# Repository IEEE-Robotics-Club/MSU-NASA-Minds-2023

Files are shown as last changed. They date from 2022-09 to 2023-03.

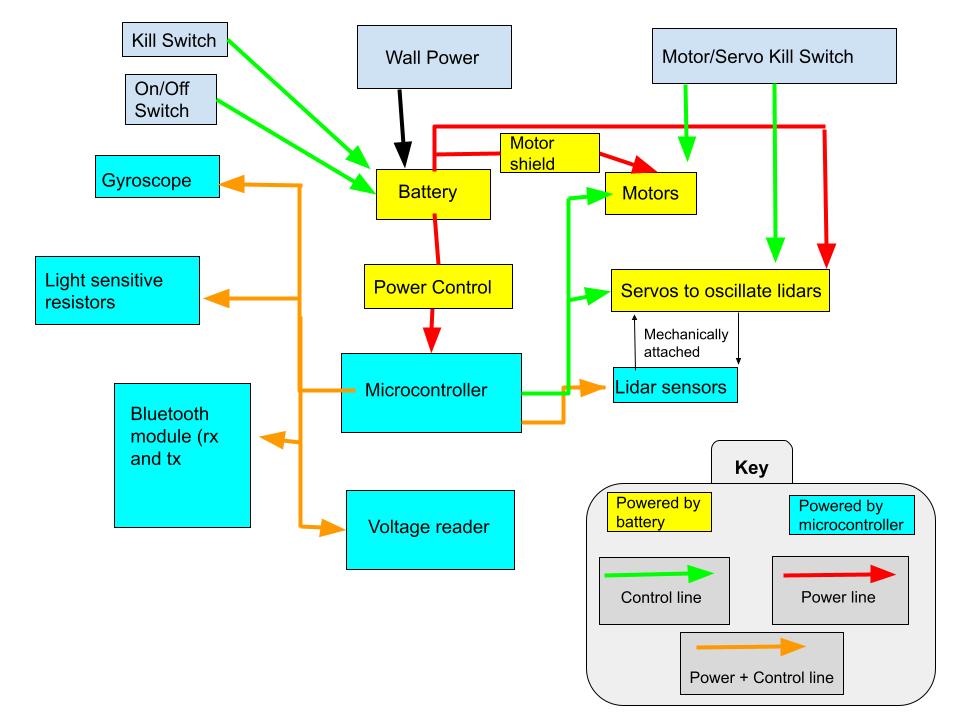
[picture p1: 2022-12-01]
Docs/iteration1/Electrical Block Diagram V2.jpg

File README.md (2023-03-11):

# MSU-NASA-Minds-2023
The code repository for the 2023 MSU NASA Minds competition. This year we will explore different cooperative imformation gathering techniques via simulation and building a homogenous robotic swarm. This repository will be split up into several different sections:

## ARGoS Robotic Swarm Simulator: 

We will be modelling and testing our system methods using ARGoS Robotic Simulator. This will serve the purpose of testing our movement algorithms and swarm logic.  

### Getting Started with ARGoS Simulator on an Ubuntu Machine:

1. Install ARGoS as per directions here https://www.argos-sim.info/core.php 

2. Clone the ARGoS-Simulations Repository and save it in a memorable place. 

3. Navigate to the repository using the terminal and run the command:

  `$ argos3 -c  Tellus-Prototype/tellus.argos

This will run the example simulation and also open the Lua editor where you can change the Robot's behaviour with a Lua Script.

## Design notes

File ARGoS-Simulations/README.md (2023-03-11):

# Getting Started with ARGoS Robotic Simulator 

After installing ARGoS Simulatior, run this command to launch the demo project:

`
$ argos3 -c  Tellus-Prototype/tellus.argos
`

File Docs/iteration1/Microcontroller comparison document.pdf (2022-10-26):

Microcontroller comparison document-

Seeed Studio XIAO nRF52840

Teensy 4.1

Pros: Teensy

- Has better software support (open source OS prebuilt on GitHub)
- Has more RAM (2 banks 512k)
- Has a FPU
- Decent hardware documentation compared to Xiao

Cons: Teensy

- Overheating with the main chip
- More expensive ($29.60)
- Sometimes no USB communication

Pros: Xiao

- Onboard bluetooth support (good for comms)
- Cheaper ($9.90)

Cons: Xiao

- No open source OS (would have to build our own)
- Poor documentation compared to teensy

Winner:

Documentation on the teensy is better compared to xiao, and the support of an OS makes it a lot better to work with. We can overcome the lack of onboard wireless support by using an external module.

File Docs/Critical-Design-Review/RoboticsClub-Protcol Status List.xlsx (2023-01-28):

Protocol lists of what is created and what is not | Protcol Flowchart Exist? | Other known names | Who made it/Where can it be Found?
Name of Protocol |  | Other name | Name and/or where it is
Boot up Calibration
Sector assignment
Agent Update |  | Swarm State Detection
Open Rescue Request
Close Rescue Request
Rescue attempt |  | Rescue Detection Protocol
Assist Path
GPR Path Generation
Collect and Store GPR
Fault Detection Protocol

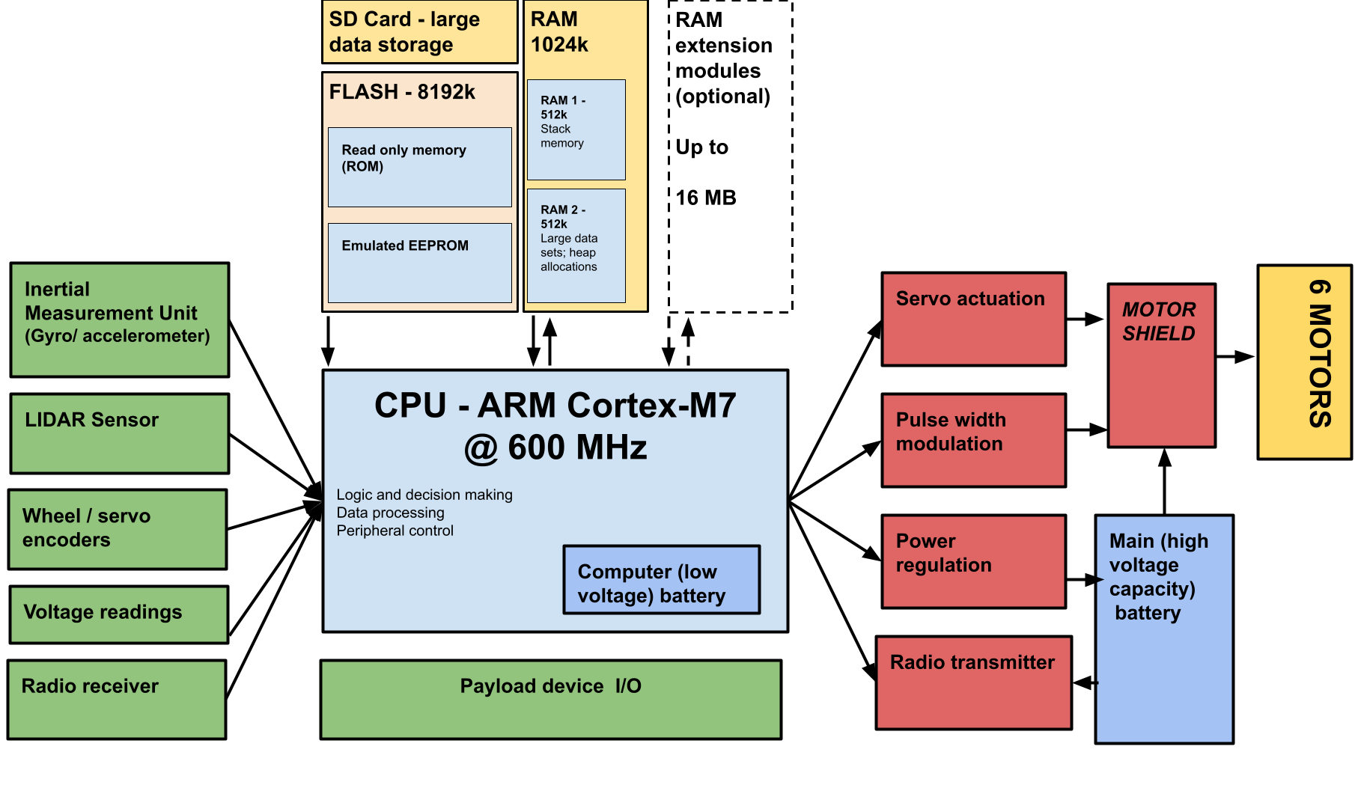
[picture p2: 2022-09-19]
Docs/iteration1/embedded systems diagram.png

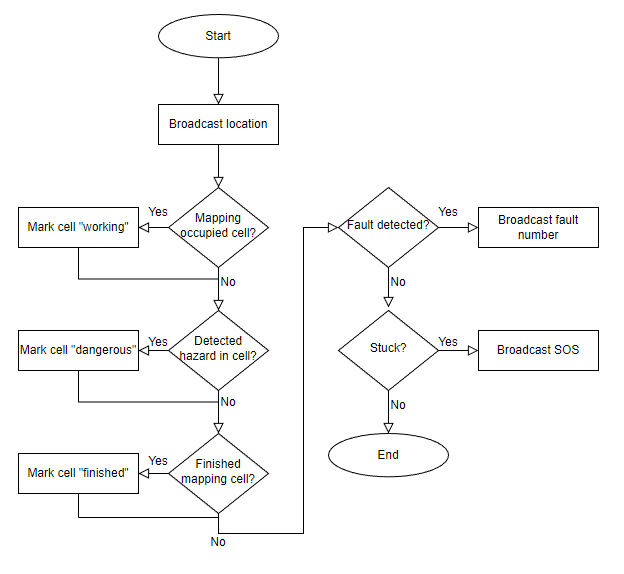
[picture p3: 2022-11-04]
Docs/iteration1/Send Communication Protocol.png

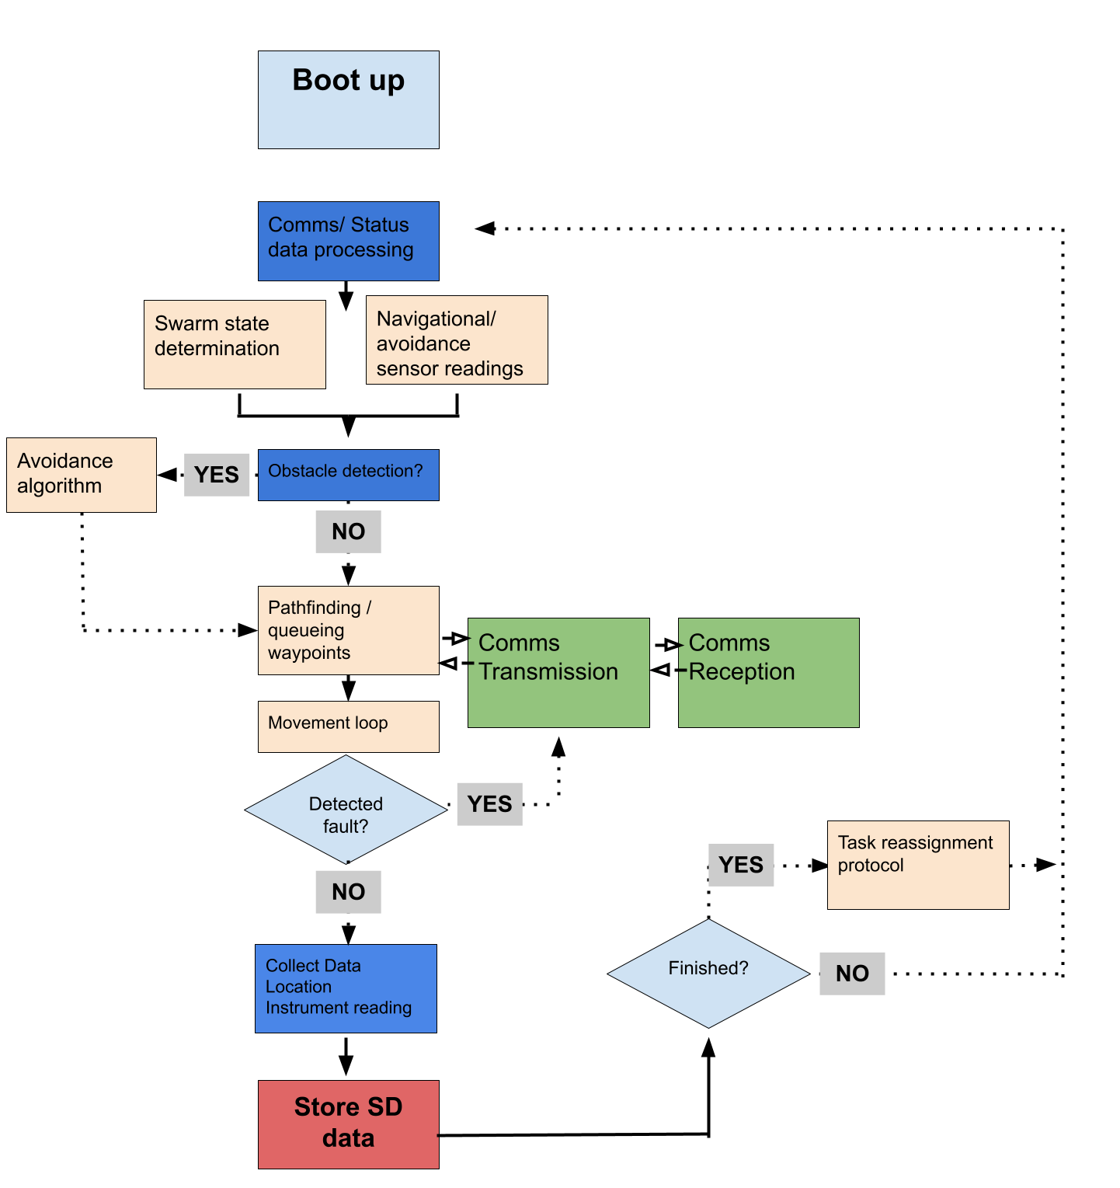
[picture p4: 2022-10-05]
Docs/iteration1/Protocol Flowchart Iteration 1.png

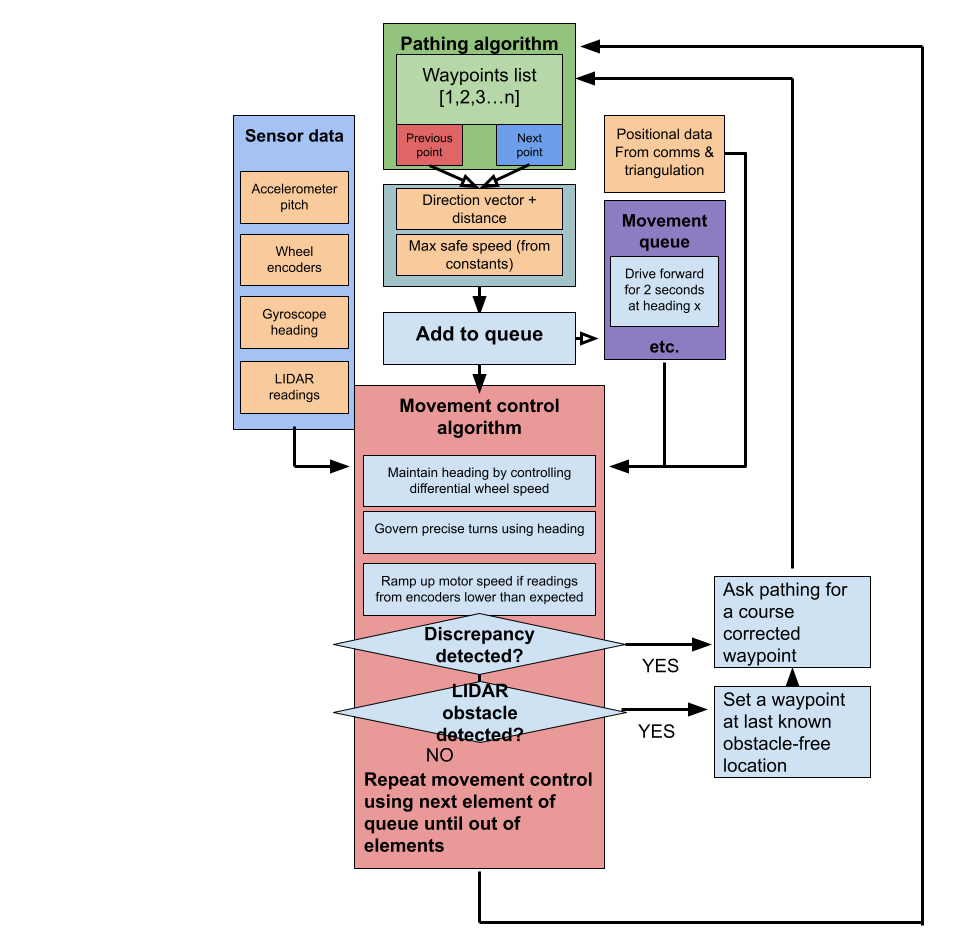
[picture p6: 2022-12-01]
Docs/iteration1/Movement control sub-protocol.png

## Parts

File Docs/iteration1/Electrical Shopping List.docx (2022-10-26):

Pack of 8 motors - $12 (https://www.amazon.com/Electric-Prewired-Intelligent-Chassis-Connector/dp/B0B19VC1VL?hvadid=598295292427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)

Speed | 18000 RPM
Item Weight | 29 Grams

8PCSTT motor robot gear motor operating voltage: 3V~12VDC (recommended operating voltage of about 6 to 8V) with 2×200mm wires

Operating Voltage: 3V~6VDC; Batch Number: Double axis 1:48; Load Current: ≤150mA (200mA MAX)

Maximum torque: 800gf cm min (3V) ; No-load speed: 1:48 (3V time)

Pack of 8 servos - $20 (https://www.amazon.com/10Pcs-Servos-Helicopter-Airplane-Controls/dp/B08KY49SFX?hvadid=475740798427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)

Weight: 9g

Stall torque: 1.8kg/cm

Operating speed: 0.1sec/60degree

Operating voltage: 4.8V

Temperature range: 0℃ ~ +55℃

Dead band width: 10us

Maximum rotation angle: 180 degrees

Gear medium: nylon

Working mode: Simulation

Circuit connection:

Yellow line (signal line)

Red line (power line)

Brown (ground)

Lipo charger $7, will need four max (https://www.adafruit.com/product/1904)

Charges 4.7v Lipo batteries of any capacity

LiPo Battery $12.5 (https://www.adafruit.com/product/2011), will need two

- Dimensions: 60mm x 36mm x 7mm / 2.4" x 1.4" x 0.3"
- Weight: 34g
- Nominal Capacity: 2000mAh ±2%
- Nominal Voltage: 3.7V
- Standard Charge Current: ~0.2C / 0.5A
- Charge Cut-Off Voltage: 4.2V
- Standard Discharge Current: ~0.2C / 0.5A
- Battery Datashee (https://cdn-shop.adafruit.com/datasheets/LiIon2000mAh37V.pdf)t

TOTAL PRICE: $85 (before tax) ~$100 after tax

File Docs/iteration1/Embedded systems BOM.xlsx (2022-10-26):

Name | Cost | Quantity | Total Cost: | $152.59
Teensy 4.1 | $34.60 | 1 | $34.60
USB | $0.00 | 1 | $0.00
SD card | $11.25 | 1 | $11.25
Pin headers | $4.99 | 1 | $4.99
Bluetooth | $20.00 | 1 | $20.00
LIDAR Module | $24.90 | 1 | $24.90
Wheel encoder x2 | $13.95 | 3 | $41.85
Motor shield | $15.00 | 1 | $15.00

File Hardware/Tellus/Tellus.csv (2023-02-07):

Comment | Designator | Footprint | LCSC
22uF | C1,C3,C5,C6,C8 | Capacitor_SMD:C_1210_3225Metric_Pad1.33x2.70mm_HandSolder | C309062
0.1uF | C2,C9 | Capacitor_SMD:C_1210_3225Metric_Pad1.33x2.70mm_HandSolder | C106103
10n | C4 | Capacitor_SMD:C_1210_3225Metric_Pad1.33x2.70mm_HandSolder | C527379
2.22uF | C7 | Capacitor_SMD:C_1210_3225Metric_Pad1.33x2.70mm_HandSolder | C76681
10K | R1 | Resistor_SMD:R_1206_3216Metric | C416174
4.7k | R2,R3,R4 | Resistor_SMD:R_1206_3216Metric | C104821
A3909 | U1,U3,U4 | Package_SO:SSOP-10_3.9x4.9mm_P1.00mm | C2653462
AMS1117-3.3 | U2 | Package_TO_SOT_SMD:SOT-89-3 | C347256

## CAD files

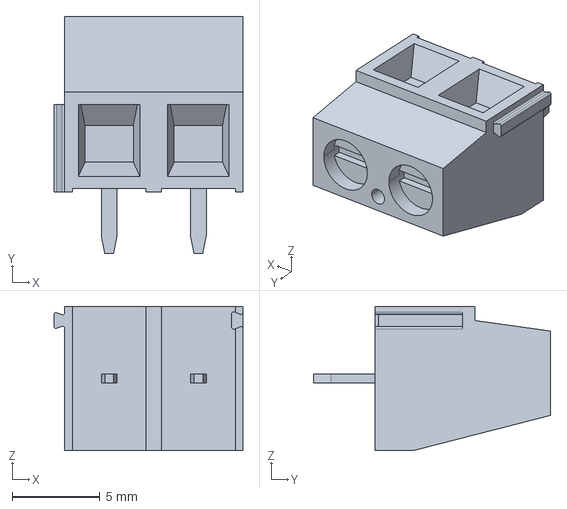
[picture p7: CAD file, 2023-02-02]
Hardware/Tellus/Terminal Block/282837-2.step
10.8 x 13.5 x 8.20 mm

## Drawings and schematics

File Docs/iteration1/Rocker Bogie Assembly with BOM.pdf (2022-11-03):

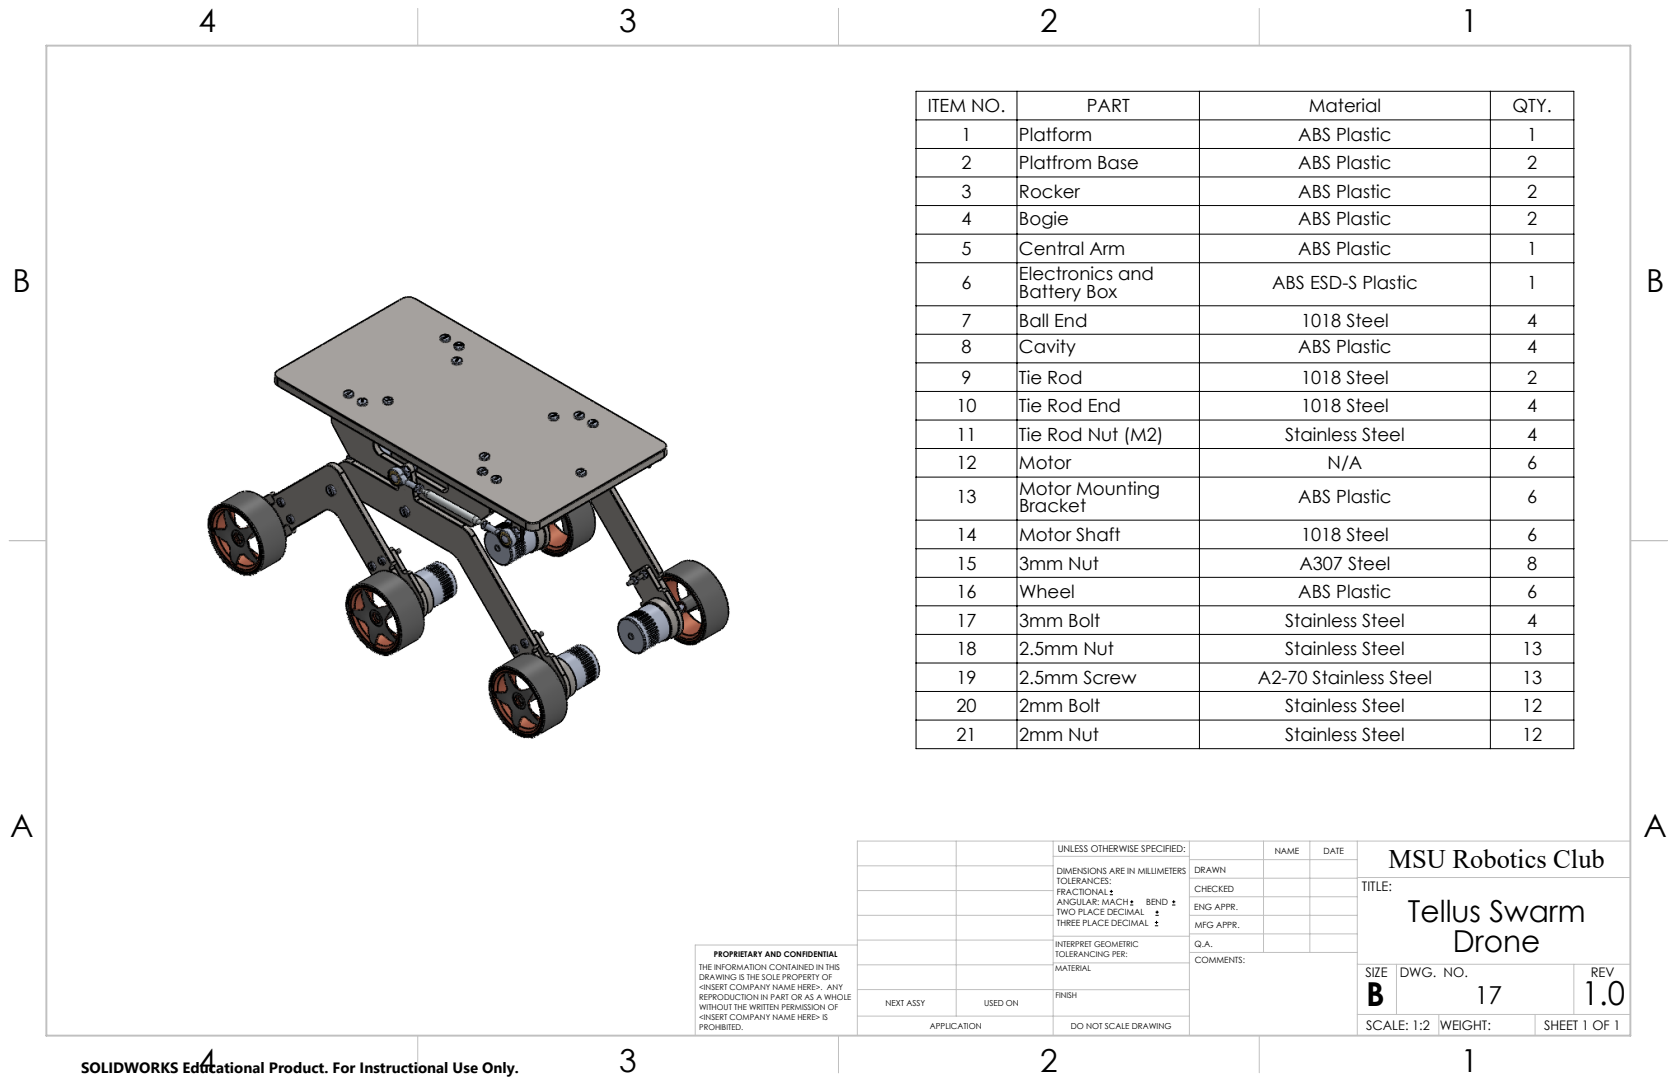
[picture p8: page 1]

ITEM NO. | PART | Material | QTY.
1 | Platform | ABS Plastic | 1
2 | Platfrom Base | ABS Plastic | 2
3 | Rocker | ABS Plastic | 2
4 | Bogie | ABS Plastic | 2
5 | Central Arm | ABS Plastic | 1
6 | Electronics and Battery Box | ABS ESD-S Plastic | 1
7 | Ball End | 1018 Steel | 4
8 | Cavity | ABS Plastic | 4
9 | Tie Rod | 1018 Steel | 2
10 | Tie Rod End | 1018 Steel | 4
11 | Tie Rod Nut (M2) | Stainless Steel | 4
12 | Motor | N/A | 6
13 | Motor Mounting Bracket | ABS Plastic | 6
14 | Motor Shaft | 1018 Steel | 6
15 | 3mm Nut | A307 Steel | 8
16 | Wheel | ABS Plastic | 6
17 | 3mm Bolt | Stainless Steel | 4
18 | 2.5mm Nut | Stainless Steel | 13
19 | 2.5mm Screw | A2-70 Stainless Steel | 13
20 | 2mm Bolt | Stainless Steel | 12
21 | 2mm Nut | Stainless Steel | 12

UNLESS OTHERWISE SPECIFIED: | | DATE | MSU Robotics Club NAME

DIMENSIONS ARE IN MILLIMETERS TOLERANCES: FRACTIONAL ANGULAR: MACH BEND TWO PLACE DECIMAL THREE PLACE DECIMAL | DRAWN

CHECKED | | TITLE: Tellus Swarm Drone

ENG APPR.
MFG APPR.

INTERPRET GEOMETRIC TOLERANCING PER: | Q.A.
MATERIAL | | SIZE B | DWG. NO. 17 | REV 1.0

PROPRIETARY AND CONFIDENTIAL
THE INFORMATION CONTAINED IN THIS
DRAWING IS THE SOLE PROPERTY OF
<INSERT COMPANY NAME HERE>. ANY
REPRODUCTION IN PART OR AS A WHOLE
WITHOUT THE WRITTEN PERMISSION OF
<INSERT COMPANY NAME HERE> IS
PROHIBITED.

NEXT ASSY | USED ON | FINISH

APPLICATION | DO NOT SCALE DRAWING | | SCALE: 1:2 | WEIGHT: | SHEET 1 OF 1

SOLIDWORKS Educational Product. For Instructional Use Only.

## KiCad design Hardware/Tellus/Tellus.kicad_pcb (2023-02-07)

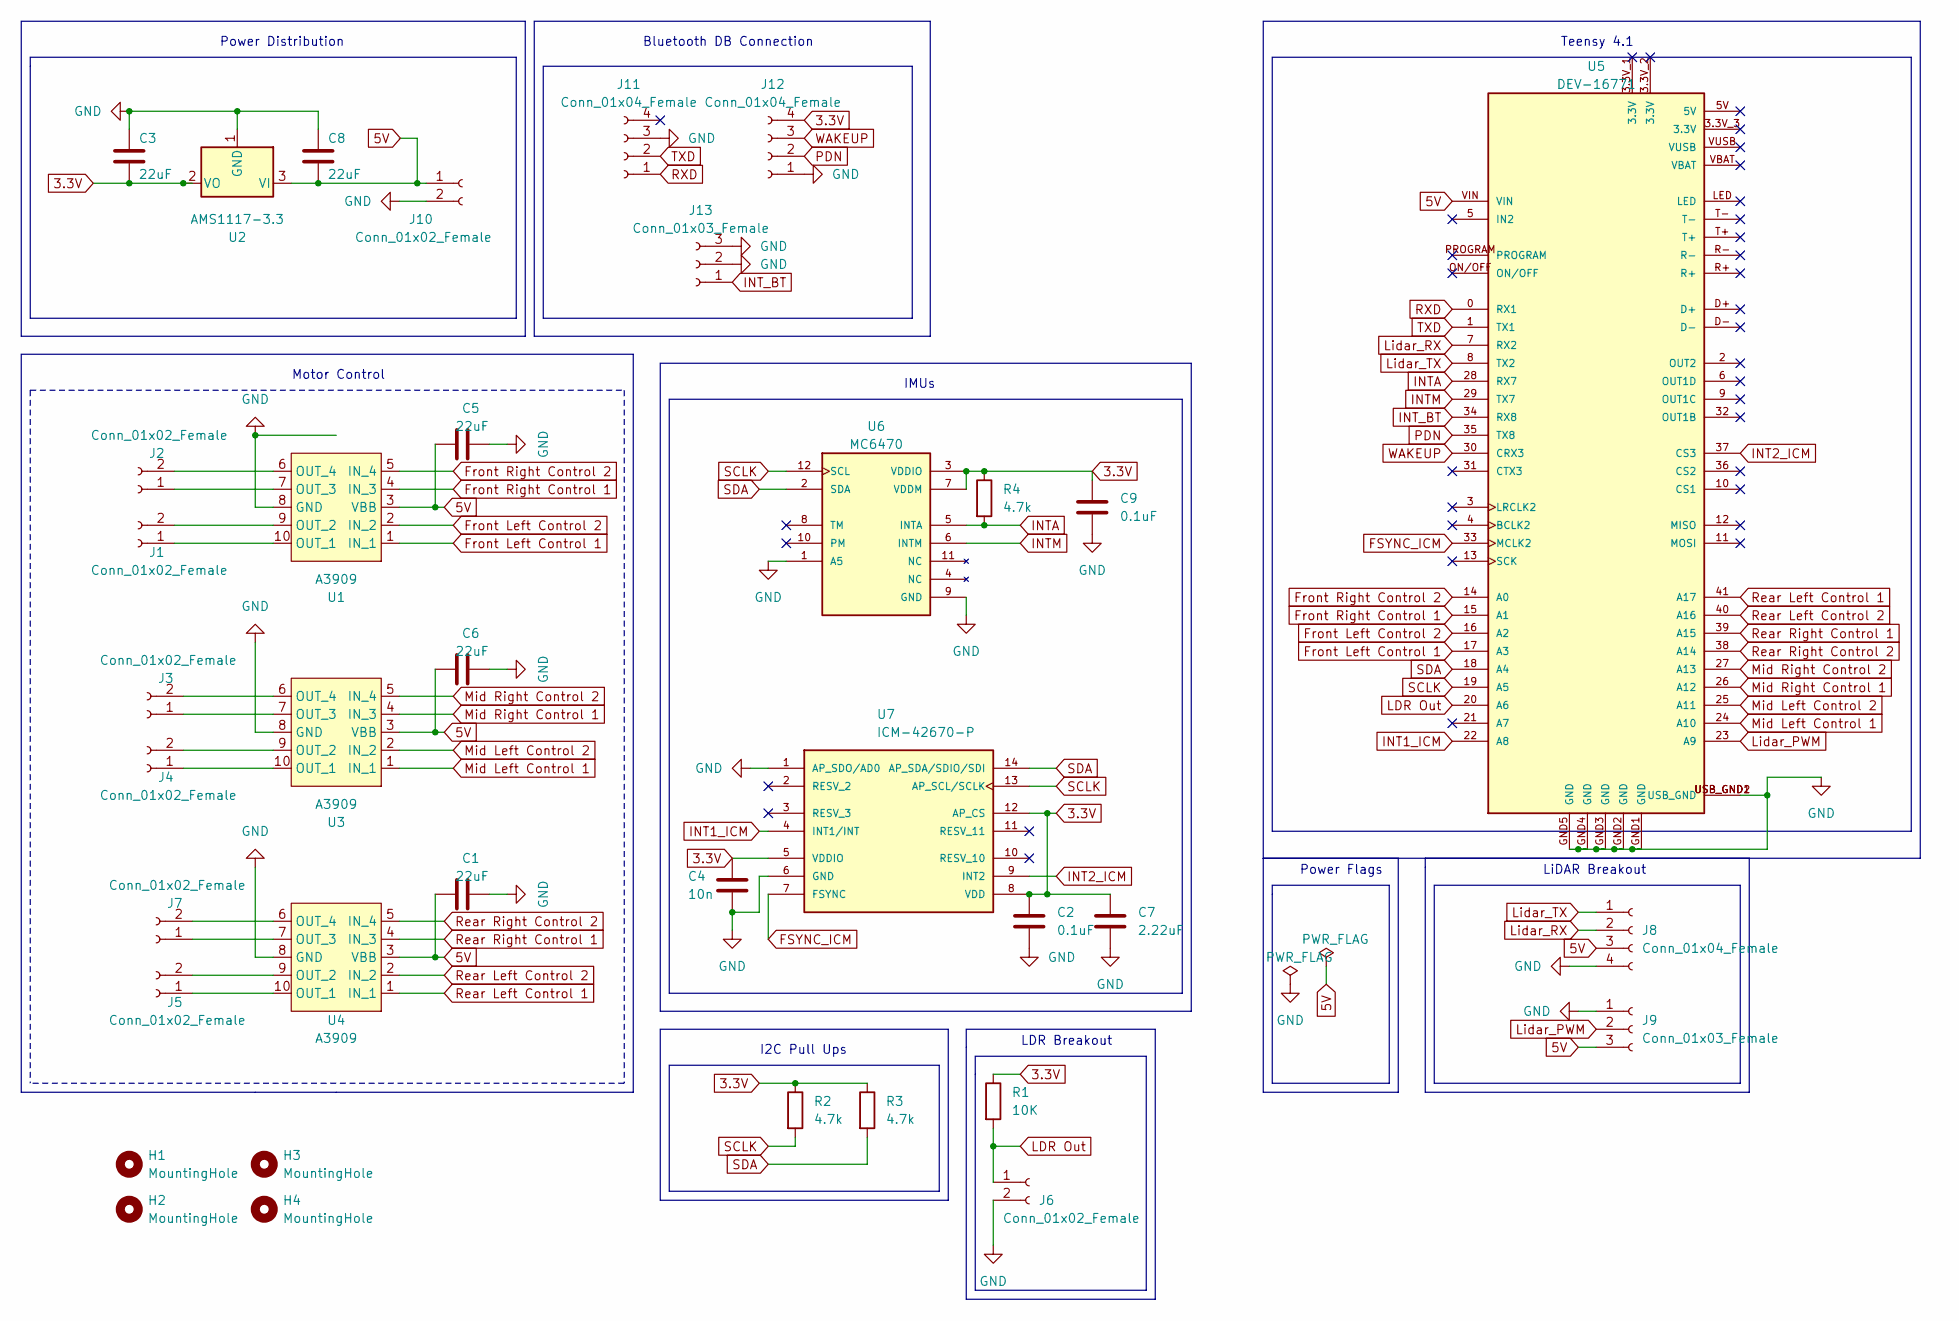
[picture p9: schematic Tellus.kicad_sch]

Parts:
C1, C3, C5, C6, C8: 22uF; C_1210_3225Metric_Pad1.33x2.70mm_HandSolder
C2, C9: 0.1uF; C_1210_3225Metric_Pad1.33x2.70mm_HandSolder
C4: 10n; C_1210_3225Metric_Pad1.33x2.70mm_HandSolder
C7: 2.22uF; C_1210_3225Metric_Pad1.33x2.70mm_HandSolder
H1, H2, H3, H4: MountingHole
J1, J2, J3, J4, J5, J6, J7, J10: Conn_01x02_Female; PinHeader_1x02_P2.54mm_Vertical
J8: Conn_01x04_Female; PinHeader_1x04_P2.54mm_Vertical
J9: Conn_01x03_Female; PinHeader_1x03_P2.54mm_Vertical
J11, J12: Conn_01x04_Female; PinHeader_1x04_P2.00mm_Vertical
J13: Conn_01x03_Female; PinHeader_1x03_P2.00mm_Vertical
R1: 10K; R_1206_3216Metric
R2, R3, R4: 4.7k; R_1206_3216Metric
U1, U3, U4: A3909; SSOP-10_3.9x4.9mm_P1.00mm
U2: AMS1117-3.3; SOT-89-3
U5: DEV-16771; MODULE_DEV-16771; PARTREV 4.1
U6: MC6470; PQFN50P200X200X100-12N; PARTREV 1.7
U7: ICM-42670-P; IC_ICM-42670-P

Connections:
3.3V: C2.1, C3.2, C4.1, C7.1, C9.1, J12.4, R1.1, R2.1, R3.1, R4.1, U2.2 (VO), U6.3 (VDDIO), U6.7 (VDDM), U7.5 (VDDIO), U7.8 (VDD), U7.12 (AP_CS)
5V: C1.1, C5.1, C6.1, C8.2, J8.3, J9.3, J10.1, U1.3 (VBB), U2.3 (VI), U3.3 (VBB), U4.3 (VBB), U5.VIN
FSYNC_ICM: U5.33 (MCLK2), U7.7 (FSYNC)
Front Left Control 1: U1.1 (IN_1), U5.17 (A3)
Front Left Control 2: U1.2 (IN_2), U5.16 (A2)
Front Right Control 1: U1.4 (IN_3), U5.15 (A1)
Front Right Control 2: U1.5 (IN_4), U5.14 (A0)
GND: C1.2, C2.2, C3.1, C4.2, C5.2, C6.2, C7.2, C8.1, C9.2, J6.2, J8.4, J9.1, J10.2, J11.3, J12.1, J13.2, J13.3, U1.8 (GND), U2.1 (GND), U3.8 (GND), U4.8 (GND), U5.GND1 (GND), U5.GND2 (GND), U5.GND3 (GND), U5.GND4 (GND), U5.GND5 (GND), U5.USB_GND1 (USB_GND), U5.USB_GND2 (USB_GND), U6.1 (A5), U6.9 (GND), U7.1 (AP_SDO/AD0), U7.6 (GND)
INT1_ICM: U5.22 (A8), U7.4 (INT1/INT)
INT2_ICM: U5.37 (CS3), U7.9 (INT2)
INTA: R4.2, U5.28 (RX7), U6.5 (INTA)
INTM: U5.29 (TX7), U6.6 (INTM)
INT_BT: J13.1, U5.34 (RX8)
LDR Out: J6.1, R1.2, U5.20 (A6)
Lidar_PWM: J9.2, U5.23 (A9)
Lidar_RX: J8.2, U5.7 (RX2)
Lidar_TX: J8.1, U5.8 (TX2)
Mid Left Control 1: U3.1 (IN_1), U5.24 (A10)
Mid Left Control 2: U3.2 (IN_2), U5.25 (A11)
Mid Right Control 1: U3.4 (IN_3), U5.26 (A12)
Mid Right Control 2: U3.5 (IN_4), U5.27 (A13)
unnamed: J1.1, U1.10 (OUT_1)
unnamed: J1.2, U1.9 (OUT_2)
unnamed: J2.1, U1.7 (OUT_3)
unnamed: J2.2, U1.6 (OUT_4)
unnamed: J3.1, U3.7 (OUT_3)
unnamed: J3.2, U3.6 (OUT_4)
unnamed: J4.1, U3.10 (OUT_1)
unnamed: J4.2, U3.9 (OUT_2)
unnamed: J5.1, U4.10 (OUT_1)
unnamed: J5.2, U4.9 (OUT_2)
unnamed: J7.1, U4.7 (OUT_3)
unnamed: J7.2, U4.6 (OUT_4)
PDN: J12.2, U5.35 (TX8)
RXD: J11.1, U5.0 (RX1)
Rear Left Control 1: U4.1 (IN_1), U5.41 (A17)
Rear Left Control 2: U4.2 (IN_2), U5.40 (A16)
Rear Right Control 1: U4.4 (IN_3), U5.39 (A15)
Rear Right Control 2: U4.5 (IN_4), U5.38 (A14)
SCLK: R2.2, U5.19 (A5), U6.12 (SCL), U7.13 (AP_SCL/SCLK)
SDA: R3.2, U5.18 (A4), U6.2 (SDA), U7.14 (AP_SDA/SDIO/SDI)
TXD: J11.2, U5.1 (TX1)
WAKEUP: J12.3, U5.30 (CRX3)

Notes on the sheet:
I2C Pull Ups
LiDAR Breakout
LDR Breakout
Motor Control
Power Distribution
IMUs
Teensy 4.1
Power Flags
Bluetooth DB Connection

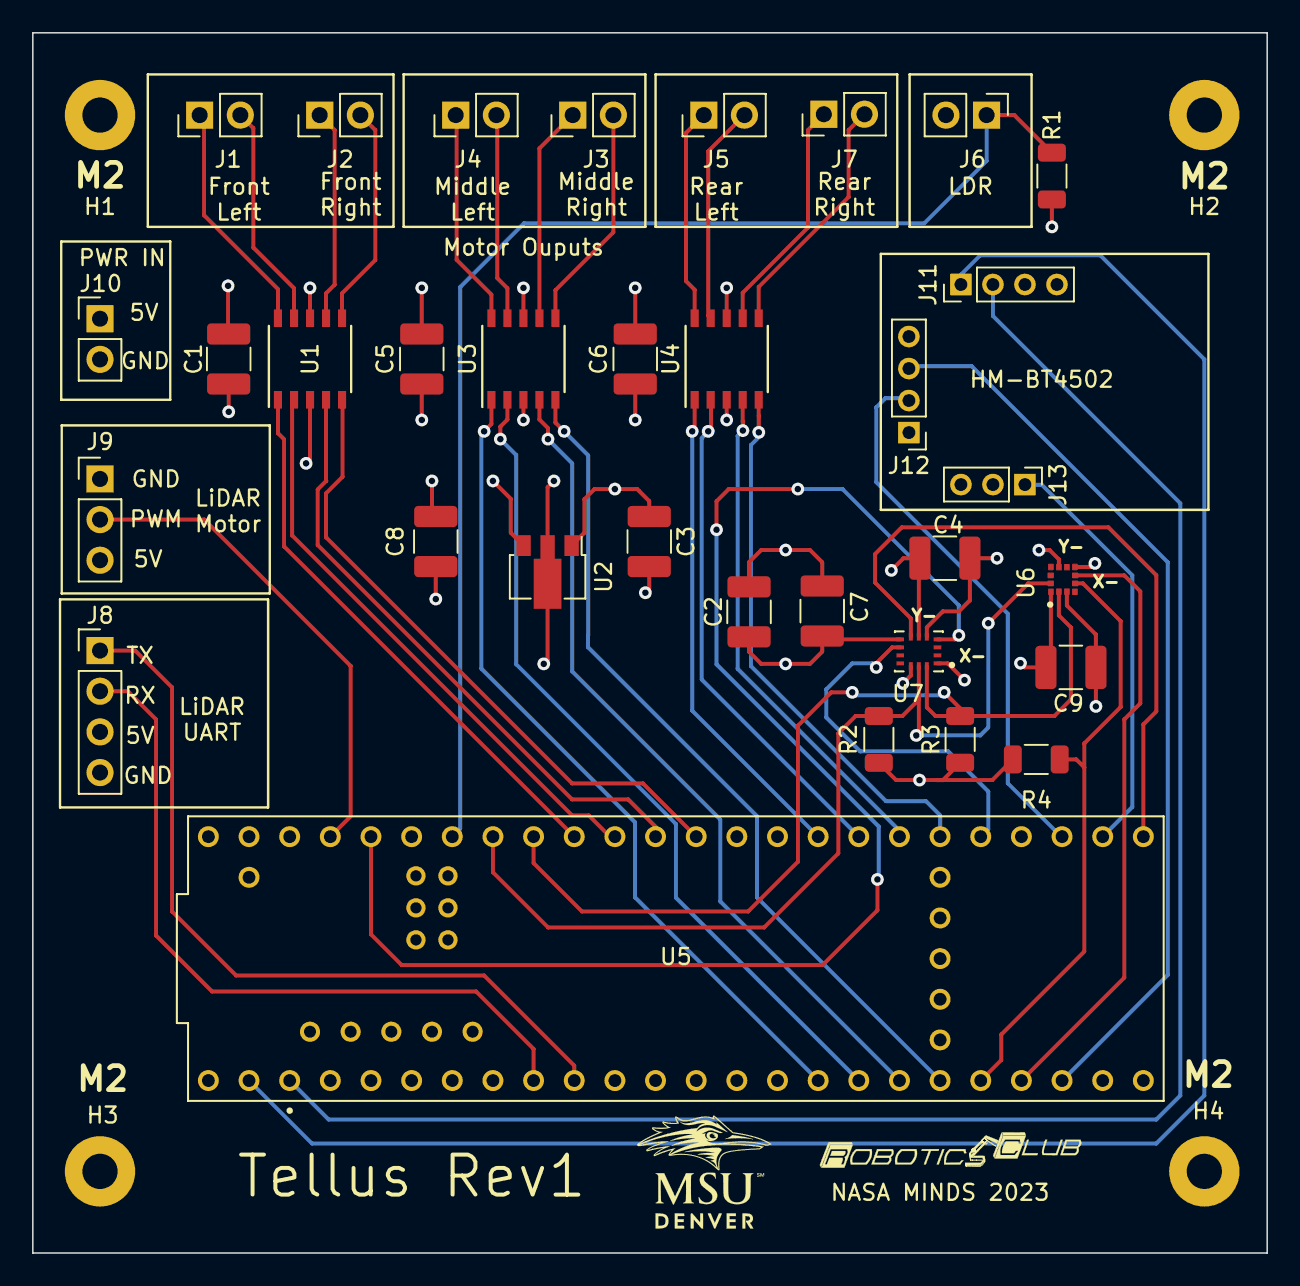
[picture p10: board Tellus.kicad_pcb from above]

Board: 4 copper layers, 77.1 x 76.2 mm, 37 parts (0 on the bottom side), 43 nets.

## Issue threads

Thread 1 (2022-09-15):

Decide on format for motor driver functions

pepsiman3, 2022-09-15:
Once we decided on what type of motors / servos we're going to be using, we can begin working on the basic API for driving them, which more advanced driving commands will build off of later.

Closed 2023-02-10.

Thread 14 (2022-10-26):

Create microcontroller comparison document

pepsiman3, 2022-10-26:
We need to figure out what microcontroller we're going with soon because of the design review deadline.

Therefore, we need to work on a document detailing the advantages and disadvantages of different microcontrollers.
Some major ones might include:

- DMA capability
- Community software support (like multithreaded OS and arduino library support)
- The extent that hardware documentation is provided
- Pin number
- Size
- Cost
- RAM
- CPU power (including FPU support)
- Native wireless capability vs. attachments

Currently under consideration, with room for more options if they are discovered:

1. Seeed Studio XIAO nRF52840
2. Teensy

TIMOTHY-HYMAN, 2022-12-01:
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
Nice

Closed 2022-12-01.

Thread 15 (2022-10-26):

Create embedded systems cost of materials doc

pepsiman3, 2022-10-26:

Fife, 2023-02-10:
BOM created, closing issue

Closed 2023-02-10.

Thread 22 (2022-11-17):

Create XML config file for Argos

pepsiman3, 2022-11-17:
Tellus Agent Requirements for ARGoS Simulation of the Swarm Agent Protocol

High Level Requirements

            Similar in size and shape to the Solid Works model

            Communication between Agents

            Control Agent’s movement

            Detect obstacles

            Read the brightness underneath Agent

Controllers

    Sensors

            Battery

            Radio

            Ground Sensor

            Wheel Encoders (Joints)

            Positioning

            Proximity

    Actuators

            Motors (Joints)

            Radio

            Differential Steering

Prototype

    Devices

            Radio

            Ground Sensor

            Proximity Sensor

Prototype Link IDs

Payload Area (Main Anchor)

LiDAR servo

Left Arm Mount

Left Rocker Arms x3 (Front, Center, Rear)

Left Wheels x3 (Front, Center, Rear)

Right Arm Mount

Right Rocker Arms x3 (Front, Center, Rear)

Right Wheels x3 (Front, Center, Rear)

Prototype Joint IDs

Left Wheels x3 (Front, Center, Rear)

Right Wheels x3 (Front, Center, Rear)

LiDAR Servo

Closed 2023-02-10.

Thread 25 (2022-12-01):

Create ARGoS simulation prototype & interface

pepsiman3, 2022-12-01:
We will need a working simulation of a swarm algorithm soon. This should ideally have some basic features such as

- [x] Low and high level motor driver functions
- [x] A pathfinding algorithm
- [x] Waypoint system
- [x] Virtual LIDAR sensor
- [ ] Basic fault detection & callbacks

These functions will be Lua-based but should ideally be structured in a way so that their function interface can be transitioned into C as painlessly as possible. This includes the use of tables as stand-ins for C structures, functions for initializers, etc

pepsiman3, 2022-12-01:
for example, https://github.com/IEEE-Robotics-Club/MSU-NASA-Minds-2023/blob/c58acfaf0b95bf55d4a456c83b780e650a0dea42/ARGoS-Simulations/MSU%20Sims/movement-MVP/motor-functions.lua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

could transitioned into similar C code,
`
void motor_init(motor_t *motor, uint8_t pin, uint16_t max_pwm);

void motor_drive(motor_t *motor, int16_t pwm);
`

Fife, 2023-02-10:
Looks like the only thing remaining on this task list is the fault detection

Fife, 2023-02-10:
Basic Fault Detection will be rolled into state machine issue

Closed 2023-02-10.

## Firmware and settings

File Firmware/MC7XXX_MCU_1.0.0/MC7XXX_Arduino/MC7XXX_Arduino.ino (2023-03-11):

#include <m_drv_console.h>
#include <m_drv_i2c.h>
#include <m_drv_mc3xxx.h>
#include <m_drv_mc70xx.h>
#include <m_drv_mc_utility.h>


//Test Sketch for communicating with the MC6470

void setup(){
    Serial.begin(9600);

    //The 70XX is the Magnetometer, While the 3XXX is the Accelerometer
    M_DRV_MC70XX_Init();
    M_DRV_MC3XXX_Init();

    //Set the Accelerometer to continuous sampling of the data
    M_DRV_MC3XXX_SetMode(1);
}

void loop(){
    //Output Arrays for the readings
    float accelOutput[3];
    float magnetOutput[3];

    //Read the sensors
    M_DRV_MC3XXX_ReadSensorData(accelOutput);
    M_DRV_MC70XX_ReadSensorData(magnetOutput);

    //Print the data to the console for testing
    Serial.println("Output Acceleration X");
    Serial.println(accelOutput[0]);
    Serial.println("Output Acceleration Y");
    Serial.println(accelOutput[1]);
    Serial.println("Output Acceleration Z");
    Serial.println(accelOutput[2]);

    Serial.println("Output Magnetic Field X");
    Serial.println(magnetOutput[0]);
    Serial.println("Output Magnetic Field Y");
    Serial.println(magnetOutput[1]);
    Serial.println("Output Magnetic Field Z");
    Serial.println(magnetOutput[2]);

}

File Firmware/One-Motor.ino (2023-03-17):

class Motor {
    private:
    int p1;
    int p2;
    int motorID;

    public:
    void sleep();
    void forward();
    void reverse();
    void brake();

    Motor(int p1, int p2, int motorID);

    void setP1(int p1);
    void setP2(int p2);
    void setMotorID(int motorID);
    int getP1();
    int getP2();
    int getMotorID();
};

void Motor::sleep() {
  digitalWrite(p1, 0);
  digitalWrite(p2, 0);
}

void Motor::forward() {
    digitalWrite(p1, 1);
    digitalWrite(p2, 0);
}

void Motor::reverse() {
    digitalWrite(p1, 0);
    digitalWrite(p2, 1);
}

void Motor::brake() {
    digitalWrite(p1, 1);
    digitalWrite(p2, 1);
}

// Mitchell's code
Motor::Motor(int p1, int p2, int motorID) {
    this->p1 = p1;
    this->p2 = p2;
    this->motorID = motorID;
    pinMode(p1, OUTPUT);
    pinMode(p2, OUTPUT);
}



Motor *myMotor = new Motor(17,16,1);
int flag= 1;



void setup() {
  // put your setup code here, to run once:

}

void loop() {
  // put your main code here, to run repeatedly:
  
  if(flag){
    myMotor->reverse(); 
    delay(2000); 

    myMotor->forward();
    delay(2000);
    
    myMotor->brake(); 
    delay(2000); 

    myMotor->forward();
    delay(2000);

    myMotor->sleep(); 
    delay(2000);
    flag = 0;   
  }

}

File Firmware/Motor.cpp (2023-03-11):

#include "Motor.h"

void Motor::sleep() {
    digitalWrite(p1, LOW);
    digitalWrite(p2, LOW);
}

void Motor::forward() {
    digitalWrite(p1, HIGH);
    digitalWrite(p2, LOW);
}

void Motor::reverse() {
    digitalWrite(p1, LOW);
    digitalWrite(p2, HIGH);
}

void Motor::brake() {
    digitalWrite(p1, HIGH);
    digitalWrite(p2, HIGH);
}

Motor::Motor(int p1, int p2, string motorID) {
    this->p1 = p1;
    this->p2 = p2;
    this->motorID = motorID;
}


// getters and setters
void Motor::setP1(int p1) {
    this->p1 = p1;
}

void Motor::setP2(int p2) {
    this->p2 = p2;
}

void Motor::setMotorID(int motorID) {
    this->motorID = motorID;
}

int Motor::getP1() {
    return p1;
}

int Motor::getP2() {
    return p2;
}

int getMotorID() {
    return motorID;
}

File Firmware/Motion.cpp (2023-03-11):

#include "Motion.h"

void Motion::forward() {
    for(int i = 0; i < 6; i++) {
        this->motors[i].forward();
    }
}

void Motion::turnLeft() {
    for(int i = 0; i < 6; i++) {
        if (this->motors[i].getMotorID % 2 == 0) {
            this->motors[i].forward();
        }
        else this->motors[i].reverse();
    }
}

void Motion::turnRight() {
    for(int i = 0; i < 6; i++) {
        if (this->motors[i].getMotorID % 2 == 0) {
            this->motors[i].reverse();
        }
        else this->motors[i].forward();
    }
}

void Motion::reverse() {
    for (int i = 0; i < 6; i++) {
        this->motors[i].reverse();
    }
}

void Motion::brake() {
    for (int i = 0; i < 6; i++) {
        this->motors[i].brake();
    }
}

void Motion::sleep() {
    for (int i = 0; i < 6; i ++) {
        this->motors[i].sleep();
    }
}

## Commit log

2022-10-05 Added protocol flowchart iteration 1
2022-10-12 Obstacle Avoidance Flowchart
    with love - tyler
2022-10-26 Fixed lua imports for the prototype example
2022-10-26 Add Embedded systems Bill of Materials
    [Embedded systems BOM.xlsx]
2022-11-17 Update Movement control sub-protocol to mention LIDAR
2022-12-01 create preliminary motor wrappers to mirror final robot code & aid in code translatability between platforms
2022-12-01 Add a speed factor for pwm values
2022-12-01 Added Controller definitions for Battery, Radios, Ground Sensor, Positioning, and Proximity sensors.
2023-01-01 Finished Tellus ARGoS Prototype
2023-01-02 Added Lidar encoder and middle wheel control
2023-01-11 Added Tellus Motherboard Rev1
    [Tellus.kicad_pcb, Tellus.kicad_sch, Tellus_Power.kicad_sch]
2023-02-02 Added Middle wheel control
2023-02-03 added middle wheels to movement functions
2023-02-03 test: swapped middle wheels in driveForward
2023-02-05 PCB Updates
    Re-Layered PCB to match Signal, PWR, GND, Signal suggestion. Cleaned up power connections, Bluetooth saddle, and LiDAR mounts.
    Fixed the following DRC Violations/Warnings:
    No Footprint assigned for Mounting holes
    - Fixed by adding them in the schematic.
    Unconnected 3.3V Terminals on Teensy
    - Fixed Symbol in schematic that had them on top of each other. The teensy spec does not recommend tying these together.
    No net assigned for Motor Driver EP
    -Modified Symbol in schematic to include the EP, and connected it to GND, as suggested in the data sheet.
    [Tellus.kicad_pcb, Tellus.kicad_sch]
2023-02-05 Added Logos
    Added MSU Logo and Robotics Club Logo to the front and back silkscreen layers
    [Tellus.kicad_pcb]
2023-02-07 Final Edits and Manufacturer File Generation
    [Tellus-B_Cu.gbl, Tellus-B_Mask.gbs, Tellus-B_Paste.gbp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]
2023-02-07 Started Lidar Mapping Library
2023-02-08 fixed middle wheel rotation for each movement function
2023-02-09 Restructured the project and lidar features
2023-02-10 Restructured the project and lidar features (#38)
2023-02-16 Started the point map data structure
    Also changed the lidar readings to be in radians instead of degrees
2023-03-01 Revisions to the lidar experiments
2023-03-01 Fixed issues with lidar setup
    Fixed problems with lidar setup including using radians instead of degrees for the {angle, distance} table.
    Also removed tellus-lidar.argos and replaced it with lidar-test.argos
2023-03-10 added first pass on Motor and Motion classes
2023-03-11 Added Arduino Libraries for the IMUs
    Ported the MC7XXX Over to C++ and added with Wire interface to work with Arduino.
